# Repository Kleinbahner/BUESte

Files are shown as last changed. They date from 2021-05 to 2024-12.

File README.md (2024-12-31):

# BUESte

## Getting parts:
Parts have been put into Reichelt.de parts baskets. Select a basket, specify the number of times you need the parts and put them in your shopping basket.
The following parts lists are available

- [bue: main pcb](https://www.reichelt.de/my/1827413)
- [bue: button boxes](https://www.reichelt.de/my/1832678)
- [bue: detectors](https://www.reichelt.de/my/1832677)
- [bue: cables](https://www.reichelt.de/my/1832680) select the cables suitable for your setup

Lists are also stored [here](https://github.com/Kleinbahner/BUESte/tree/main/doc/reichelt)

## Manuals:
Manual for main pcb assembly: [main pcb manual](https://github.com/Kleinbahner/BUESte/blob/main/doc/Manual%20(DE)%20Bahn%C3%BCbergang%20Platine%20v2.pdf)

Manual for boxes: [boxes manual](https://github.com/Kleinbahner/BUESte/blob/main/doc/Manual-DE-Box.pdf), [drilling template](https://github.com/Kleinbahner/BUESte/blob/main/doc/drill%20template%20bue.pdf)

Manual for detector: to follow

## Software

Manual for programming the Arduino: [Arduino programming](https://github.com/Kleinbahner/BUESte/blob/main/doc/Programmierung%20Arduino%20f%C3%BCr%20Bahn%C3%BCbergangssteuerung.pdf)

## Components
The railway crossing control unit consists of different components that can can be combined in various ways in order to suit the actual module layout requirements. The components will be described in more detail in the following sections.

### Mainboard

The main board is permanently installed near the railroad crossing. All other components are connected to the main board.

Main board v1 Main board v2

The flashing light signals for the railway crossing and the servos for the fences can be connected via terminal blocks. The control inputs are connected to further terminal blocks. There is also an amplifier for connecting a loudspeaker. The sounds can be stored on a microSD card. Power is supplied via an USB socket.

The two RJ45 sockets are used to connect the other components via a looped-through cable. All components can be connected to the same cable in any order. Star cabling is also possible. Alternatively, the inputs and outputs can also be connected directly to the terminal blocks if they are installed in the same module.

#### Pin assignement
All components must be connected to the main board. It has a number of screw and plug connections for this purpose. Ideally, the main board should be mounted near the railroad crossing itself so that many components such as the flashing signals, the light barrier for clear signaling and the loudspeaker can be connected directly. The following illustration provides an overview of the connection options.

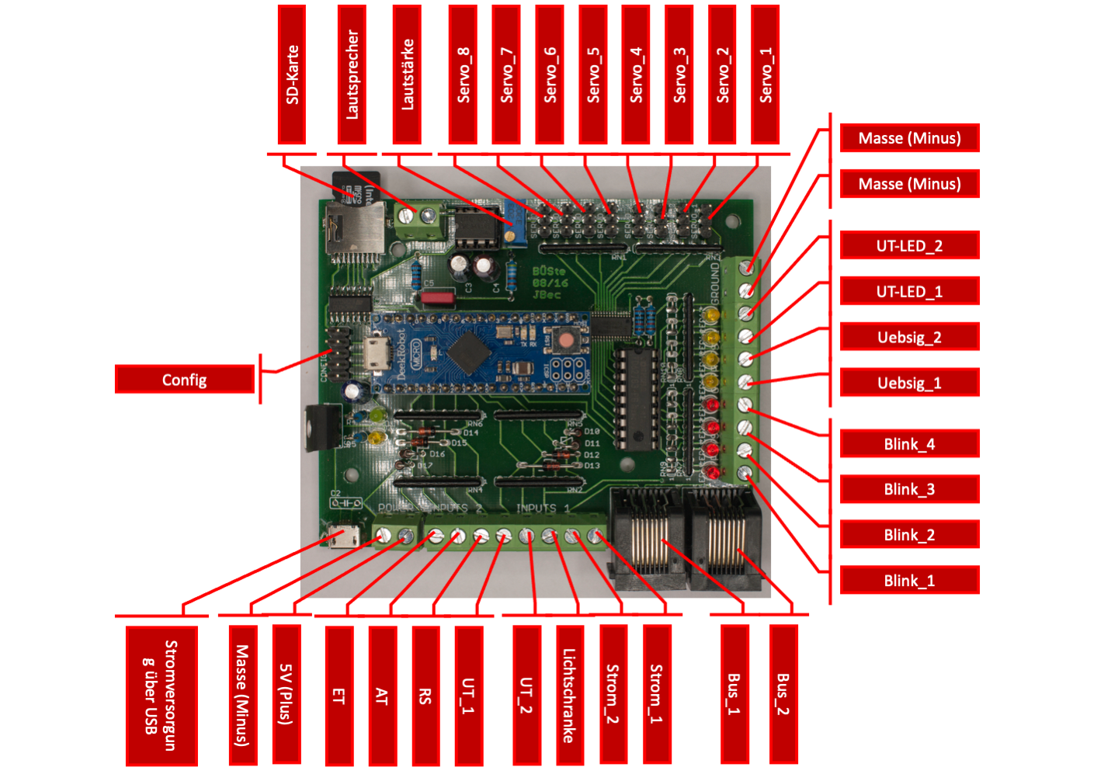
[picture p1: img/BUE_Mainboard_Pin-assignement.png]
Pin assignement main board v1
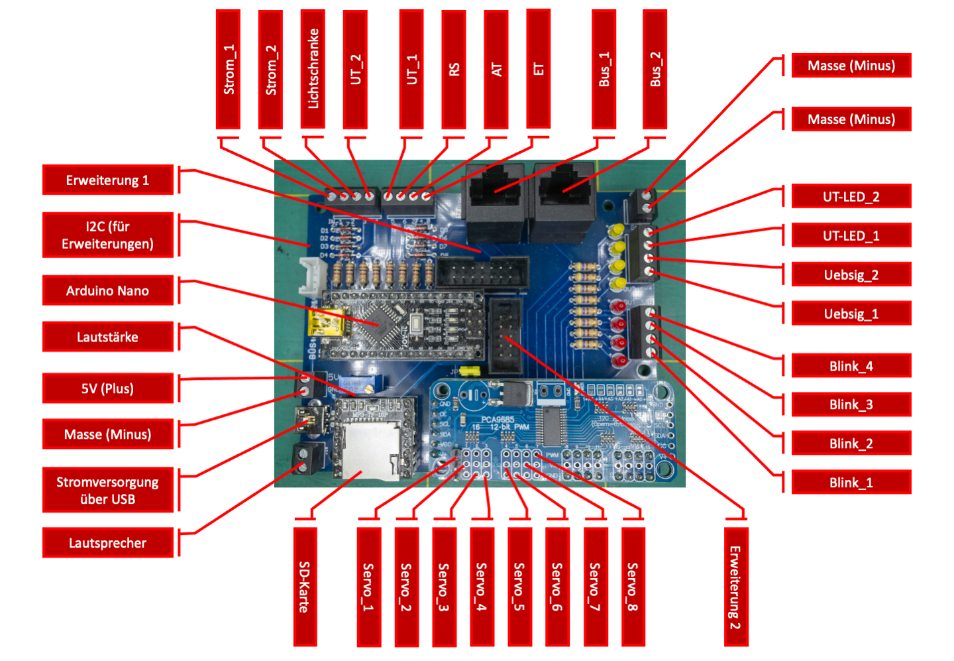
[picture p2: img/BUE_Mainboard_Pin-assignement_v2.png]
Pin assignement main board v2
 

The available signals and their meaning are listed here in detail. The output signals for the LED are driven with 5V. Corresponding series resistors must be added yourself!

| Signal | Direction | Activation | Purpose |
| --- | --- | --- | --- |
| Loudspeaker | output | - | Connections for a small passive loudspeaker, maximum 1W |
| Servo_1 ... Servo_8 | output | Servo connections for the fences. Pin assignement (from boarder of PCB): - , +, pulse |
| UT-LED_1 | output | LED is on if the current sensor on the left track is disabled by the UT push button |
| UT-LED_2 | output | LED is on if the current sensor on the right track is disabled by the UT push button |
| Uebsig_1 | output | LED for the flashing signals of the left track |
| Uebsig_2 | output | LED for the flashing signals of the right track |
| Blink_1 ... Blink_4 | output | Flashing signals for the railroad crossing.  Blink_1 and 2 are phase shifted to Blink_3 and 4 |
| Bus_1 | output | Signals to attached remote components on the left track |
| Bus_2 | output | Signals to attached remote components on the right track |
| Strom_1 | input | LOW active | Input for the current sensor of the left track |
| Strom_2 | input | LOW active | Input for the current sensor of the right track |
| Lichtschranke | input | HIGH active | Input for the light barrier for clear signaling of the railroad crossing |
| UT_1 | input | LOW active | Input to temporary deactivate the current sensor on the left track |
| UT_2 | input | LOW active | Input to temporary deactivate the current sensor on the right track |
| RS | input | LOW active | Input for the "Rangierschalter" (RS) |
| AT | input | LOW active | Input for the disable push button (AT) |
| ET | input | LOW active | Input for the enable push button (ET) |
| USB Power | input | - | Power supply for the circuit. A power bank is recommended to be independent of outlets. |
| 5V | output | - | Supply voltage for light barrier |
| Masse | - | - | Common potential for push buttons |
| Config (only v1_0) | - | - | Actually not used. Can be used for further extensions. |
| I2C (only v2_0) | - | - |  I2C bus of the arudino. For further extensions. |
| Erweiterung 1 (only v2_0) | - | - | Unused pins of the arduino. Actualy not used. |
| Erweiterung 2 (only v2_0) | - | - | Unused pins of the arduino. Actualy not used. |
| SD-Karte | - | - | Slot for SD card. The card has to contain the WAV file for the signal sound. Attention: There has to be a card in the slot with a WAV file called "ding.wav" in the main directory. Otherwise the control unit will not work! |

#### Assignement of the bus cable
A bus is used to connect the components further away from the main board. All the required signals are routed in a single multi-core cable. An RJ45 cable is used for this. Starting from the main board, all components are connected to each other. The boxes have three sockets and can therefore be used as splitters. All sockets are of equal value. The cabling can be carried out in any combination. Only the left and right sections need to be differentiated as the disable buttons, the sensors and the supervision signals are direction dependent. Examples of wiring can be found below under examples.

The socket is assigned as follows (view into the socket):

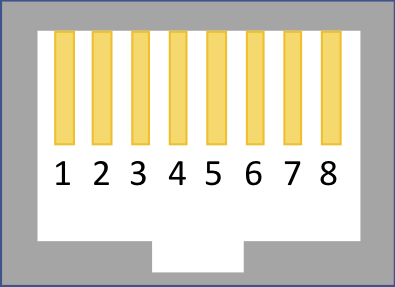
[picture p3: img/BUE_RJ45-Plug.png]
Bus socket


| Pin | Function |
| --- | --- |
| 1 | Ground |
| 2 | Enable push button (ET) |
| 3 | Disable push button (AT) |
| 4 | Shunting switch (RS) |
| 5 | Disable current sensor push button (UT) |
| 6 | LED to mark disabled current sensor |
| 7 | LED for supervision signal. Blinks in phase with flashing light signal |
| 8 | Current sensor |

### Enable box
For manual operation of the railraod crossing a small box is needed. It contains the Enable (ET) and Disable (AT) push buttons as well as a shunting switch. The shunting switch can be equiped with an LED that blinks in phase with the flashing light signal to mark its use.

Einschaltbox

The box can be attached to modules using the well know FREMO-Clamps. The box contains a hole for that purpose.

The connection from the box to the mainboard is through a RJ-45 cable (straight) as it is known from computer networks. Each box has three equal sockets. Thus it can also be used as splitter for cabling.

Backside of box

To ease the cabling inside the box, a small PCB has been designed. It fits perfectly in the boxes used and provides space for three RJ-45 sockets. In addition it provides soldering points for the push buttons and the LEDs.

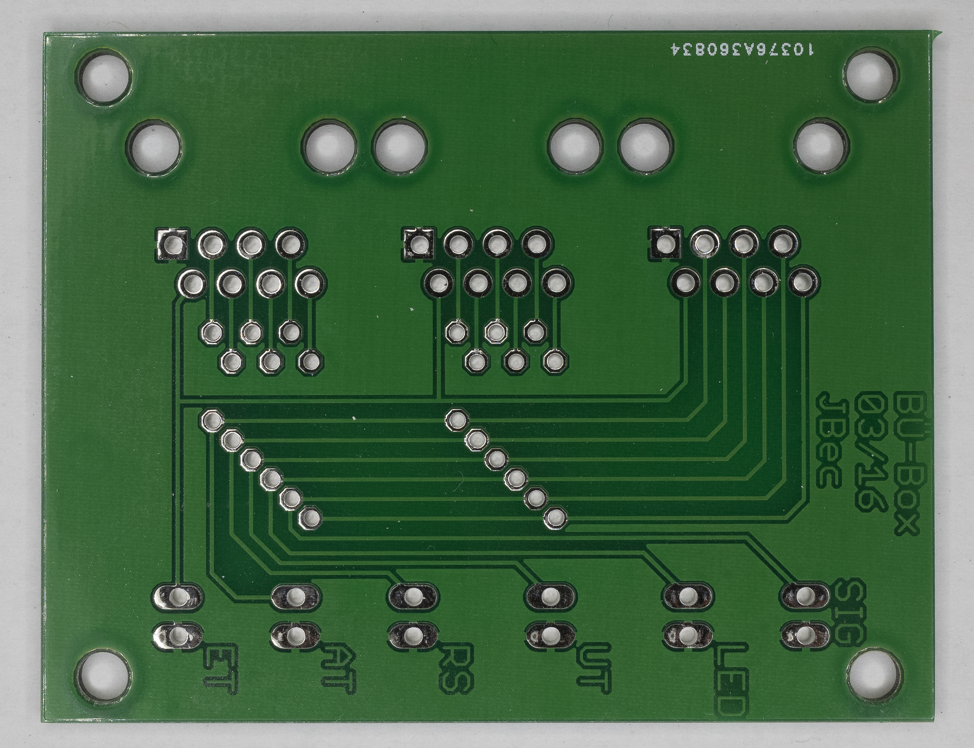
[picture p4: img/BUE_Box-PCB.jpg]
PCB for boxes


### Current sensor
The current sensor is based on the design of Reinhard Müller [http://dcc-mueller.de/wire4dcc/sensor_d.htm](http://dcc-mueller.de/wire4dcc/sensor_d.htm), that has been expanded with a RJ-45 socket for the crossing cabling system.

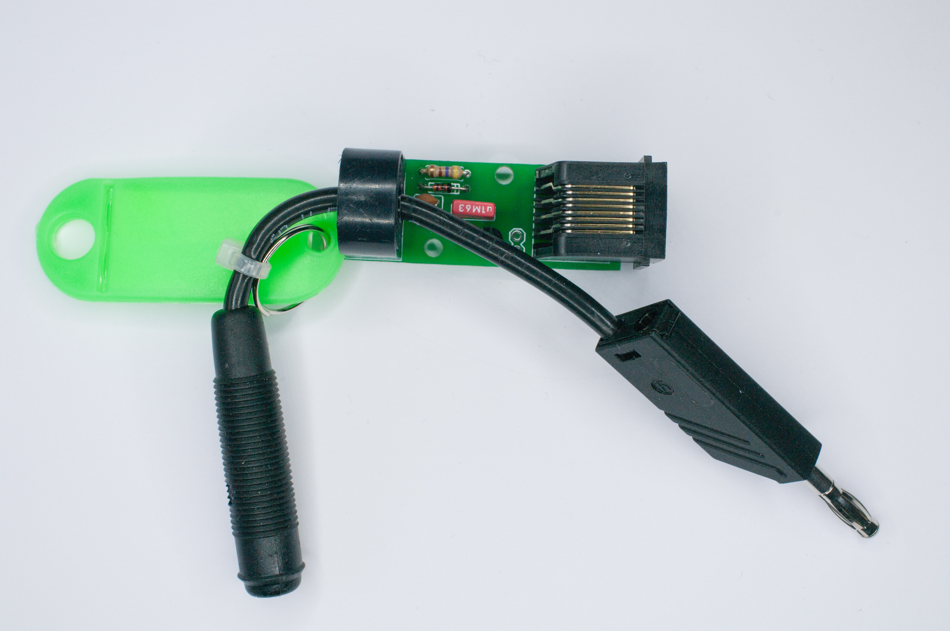
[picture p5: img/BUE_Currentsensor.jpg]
Current sensor


The purpose of the current sensor is the detection of an approaching train. In order to do that one rail of a module is isolated from the neigboring modules (module interconnection cable not pluged in). This rail is then supplied through the current sensor that is attached to the neigboring module. There are no changes of the modules required.

### Sensor box
Near to the current sensor, a sensor box can be attached to the modules using FREMO-clamps. The box can also serve als signal splitter.

Sensor box

The main purpose of this box is to provide the disable button near to the current sensor. By pressing the push button, the current sensor will be disabled for a give time period. A disabled current sensor is signaled by the LED in the box. Deactivation of the sensor can be necessary if there are shunting activities ongoing that would touch the module with the sensor without the need to close the railway crossing.

### Supervision signal
The engine driver needs to know if the railraod crossing is correctly enabled. That is the purpose of the supervision signal that is placed after the current sensor that turns the railroad crossing on. If the railroad crossing is enabled the signal will be blinking.

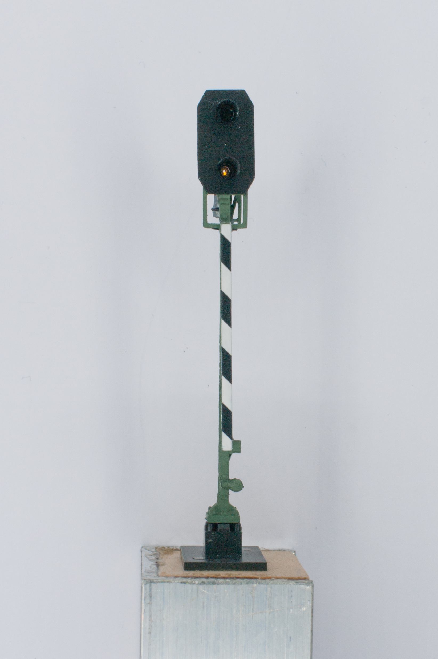
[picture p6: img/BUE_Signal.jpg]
Supervision signal


The supervision signal is placed in a Wattenscheider signal carrier and thus can be placed in any module with the propper Wattenscheiderslot. The signal is connected to the main board using an RJ45-socket. If an additional marker light should be realised, there has to be a sperate power supply. This can for example be done by including a battery and a voltage regulator in the signal carrier.

## Module setup
The components presented before allow for a flexible setup. Two example setups will be presented here.

### Railraod crossing on open track
The most simple case is a railway crossing on clear track. There the main board is integrated in the module which contains the railway crossing and crossing lights. The flashing signal lights, maybe existing fences and the speaker are then directly connected to the main board. Left and right of the railraod crossing on the module at a sufficient distance a sensor module is used. One rail will be isolated from the other modules and will be supplied through a current sensor. The sensor is connected to the main board using RJ45-cables.

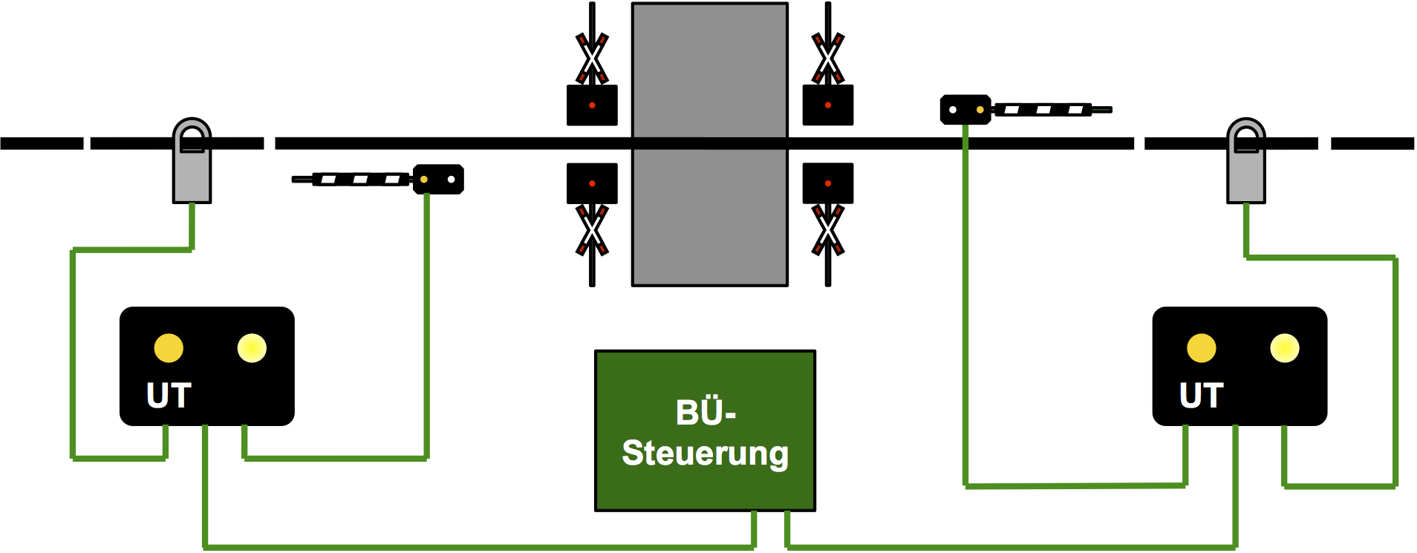
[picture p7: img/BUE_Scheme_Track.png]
Setup at free track


To connect the supervising signals it is recommended to install a sensor box near to every current sensor. The boxes are then used as splitters to connect both the current sensor and the signal.
In this setup the railroad crossing is controlled only by the trains, no interaction of the driver is required.

### Railroad crossing at the end of a station
The situation gets more complex if the railroway crossing is located at the end of a station where trains stop. In this case the railroad crossing can not only be automatically engaged by a current sensor at the side of the station. This could be the case if a train approaches to station to make sure that the crossing is stil secured if the train does not correctly stop at the platform.

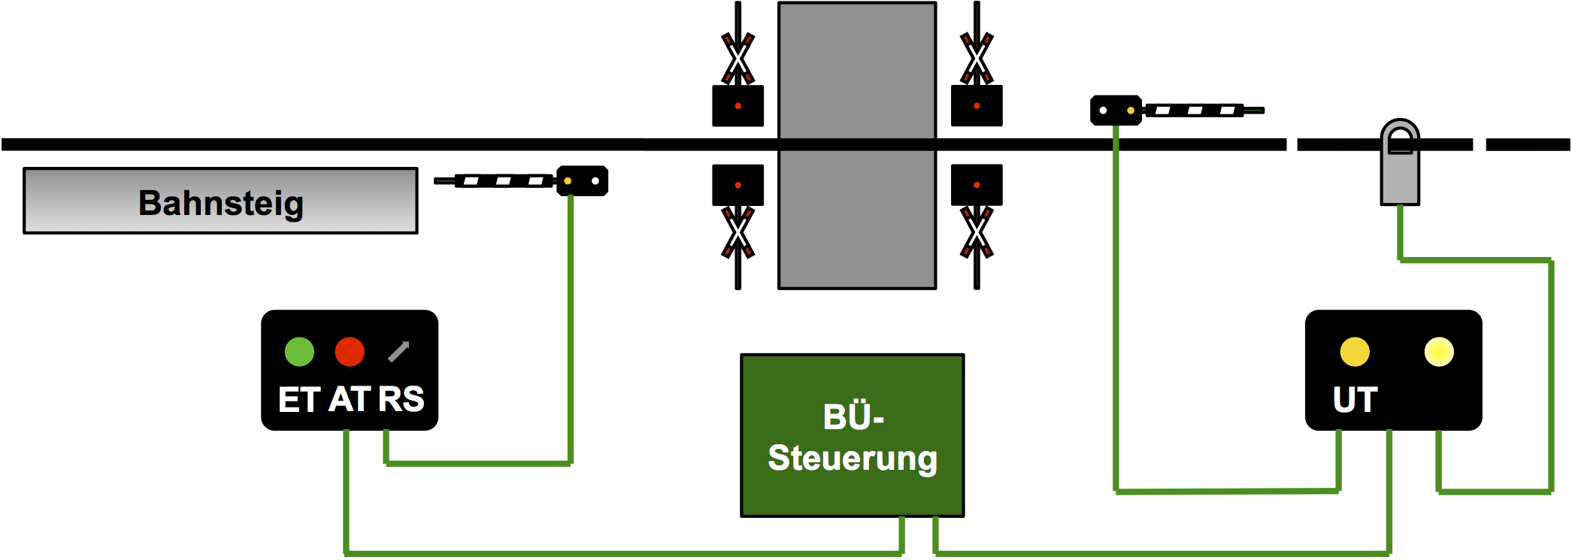
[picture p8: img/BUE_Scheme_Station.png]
Setup in station


As soon as the trains stops, the railway crossing will be deactivated manually using the Einschaltbox to allow road users to use the crossing when the train is stooped at station. Before the trains continue their journey, the crossing has to be enabled again manually. Therefore an Einschaltbox is required.
In addition the box contains the shunting switch. This is switched on if there are shunting activities ongoing that will involve the railway crossing. The lights are then permanently switched on and will only turn off after the shunting switch has been switched off.

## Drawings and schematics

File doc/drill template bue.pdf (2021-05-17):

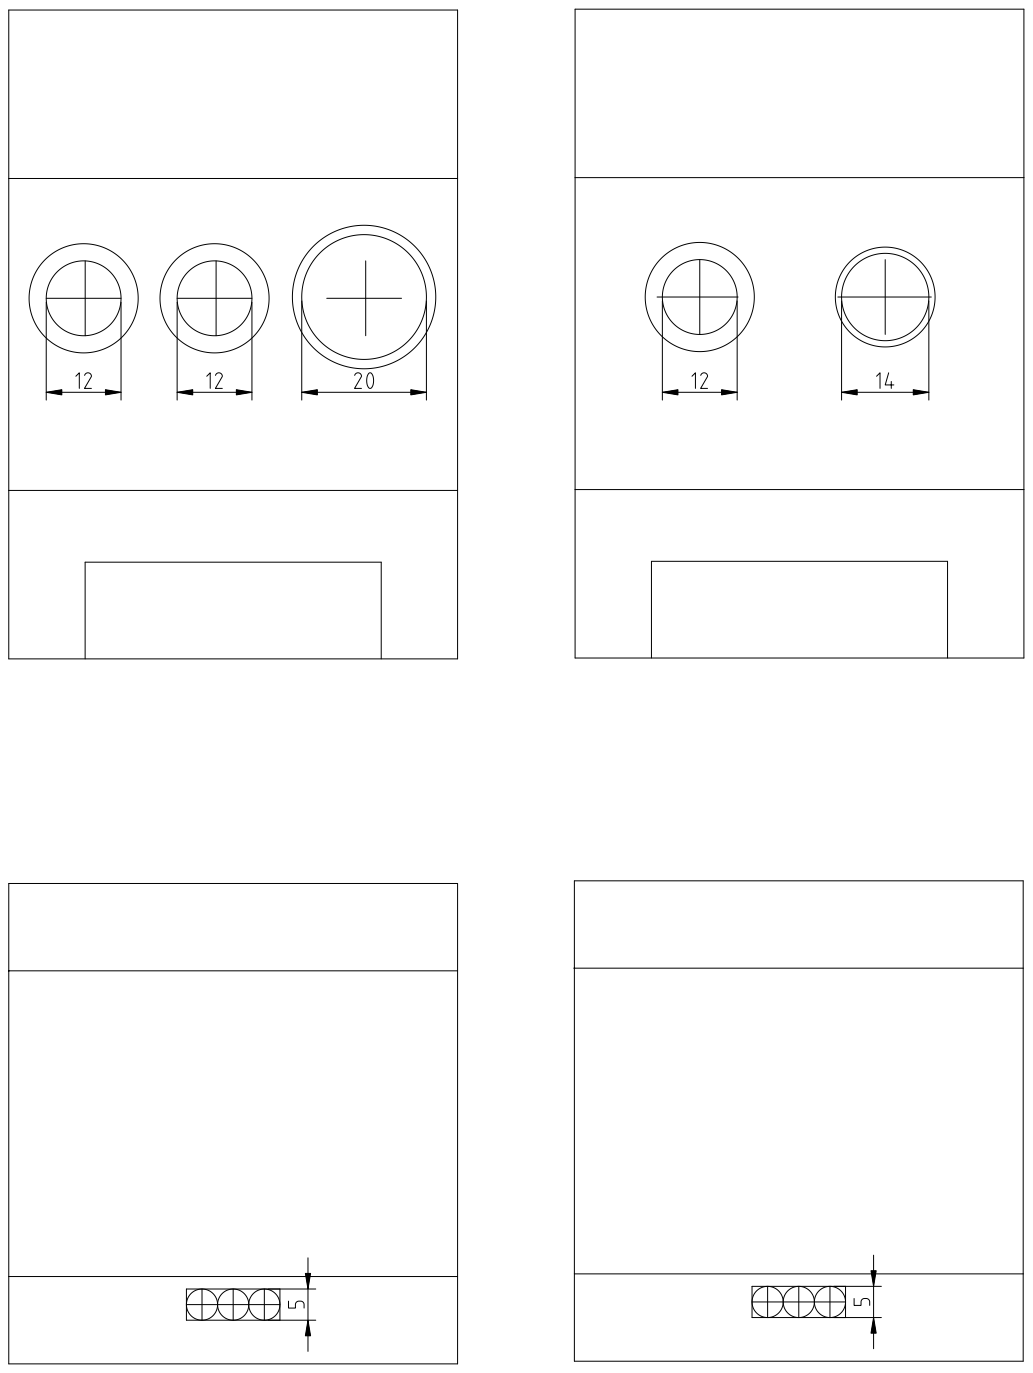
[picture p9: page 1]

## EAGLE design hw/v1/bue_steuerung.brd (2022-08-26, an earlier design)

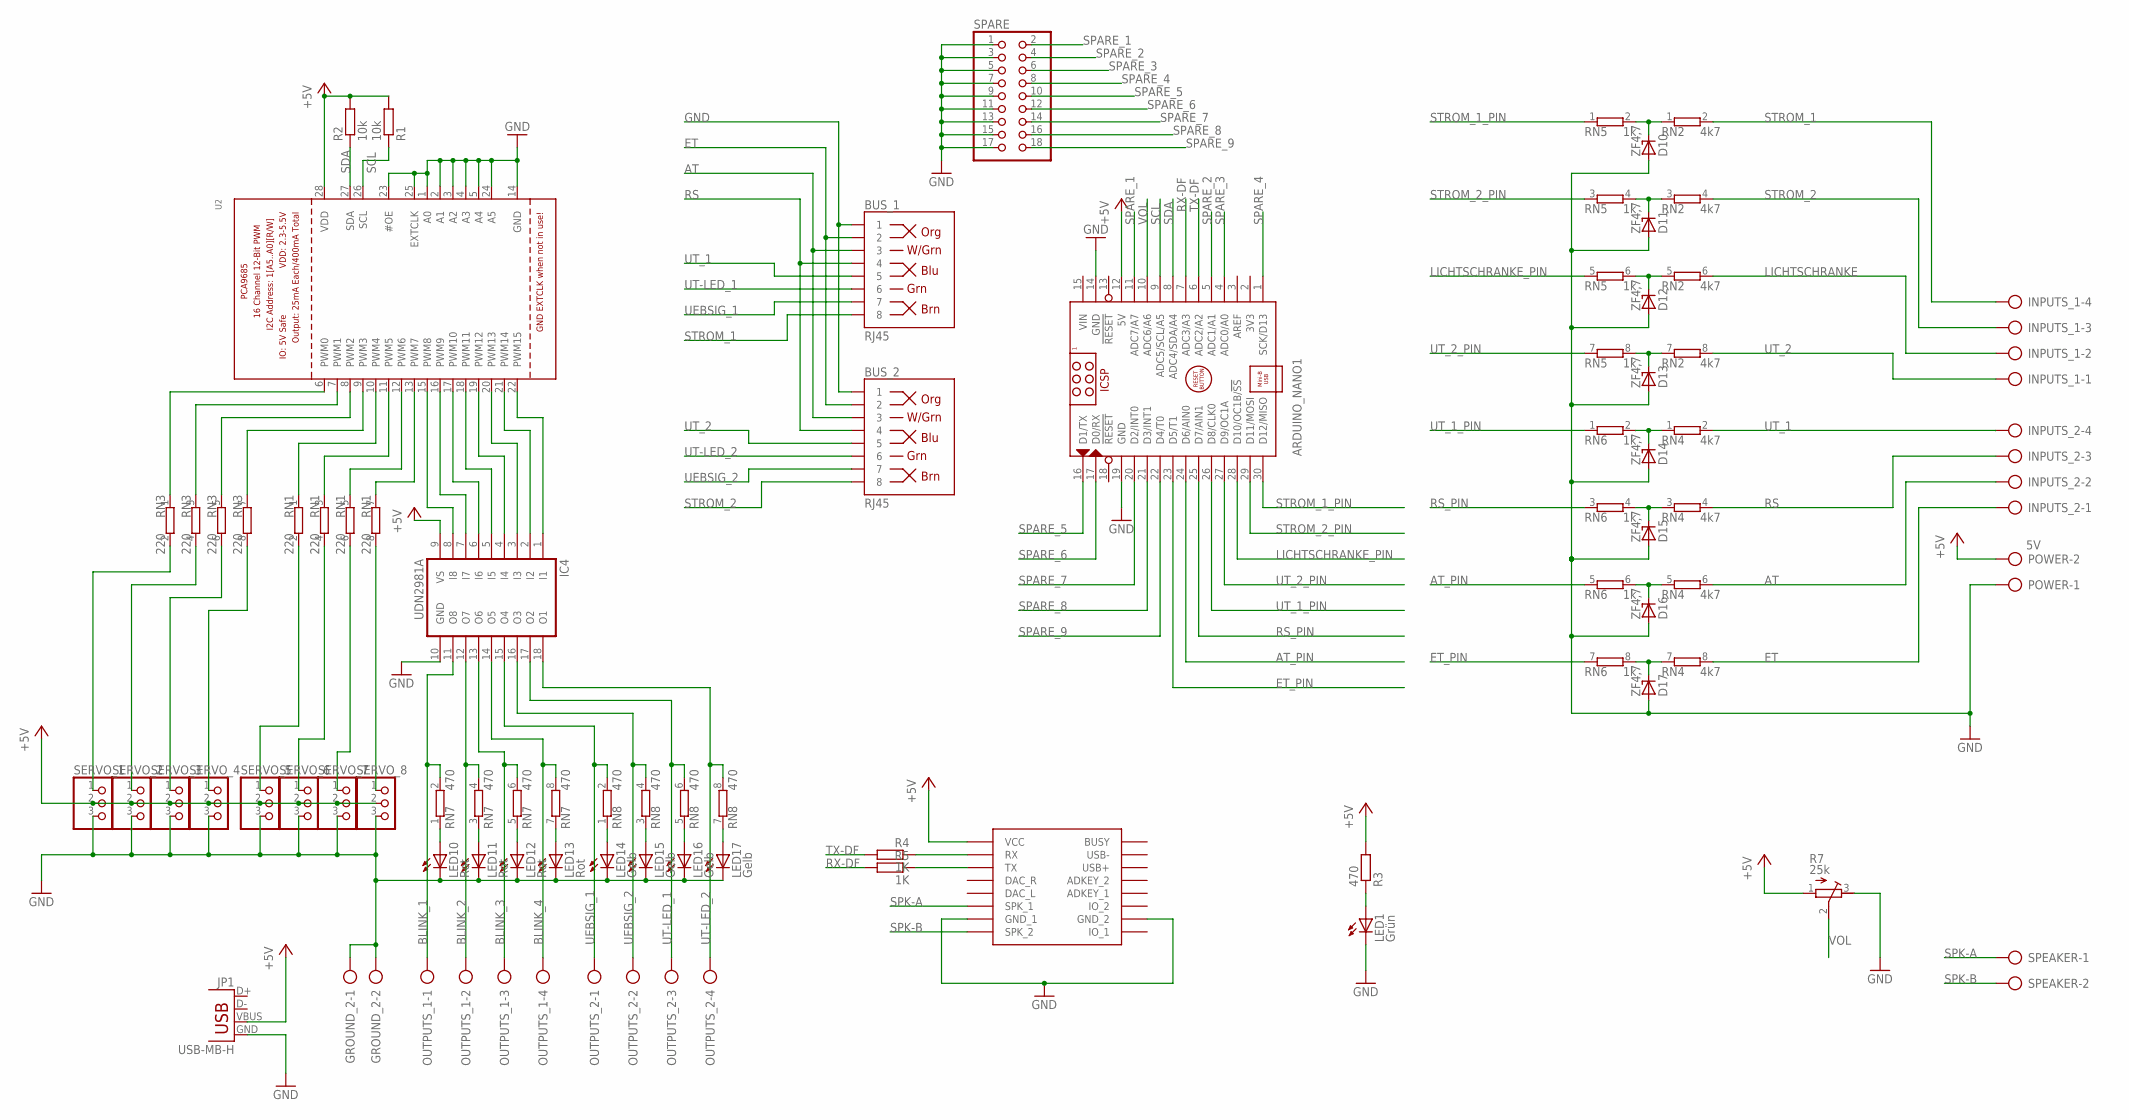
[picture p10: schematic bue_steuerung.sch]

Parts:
ARDUINO_NANO1: ARDUINO_NANO
BUS_1, BUS_2: RJ45; RJ45-8
D10, D17: ZF4,7; ZDIO-2.5
D11, D16: ZF4,7; ZDIO-5
D12, D15: ZF4,7; ZDIO-10
D13, D14: ZF4,7; ZDIO12.5
GROUND_2: AK500/2
IC4: UDN2981A; DIL18
INPUTS_1, INPUTS_2: AK500/4
JP1: USB-MB-H
LED1: Grün; LED3MM
LED10, LED11, LED12, LED13: Rot; LED3MM
LED14, LED15, LED16, LED17: Gelb; LED3MM
OUTPUTS_1, OUTPUTS_2: AK500/4
POWER: 5V; AK500/2
R1, R2: 10k; 0207/10
R3: 470; 0207/10
R4, R5: 1K; 0207/10
R7: 25k; RTRIM64Z
RN1, RN3: 220; SIL8
RN2, RN4: 4k7; SIL8
RN5, RN6: 1k; SIL8
RN7, RN8: 470; SIL8
SERVO_1, SERVO_2, SERVO_3, SERVO_4, SERVO_5, SERVO_6, SERVO_7, SERVO_8: PINHD-1X3; 1X03
SPARE: PINHD-2X9; 2X09
SPEAKER: AK500/2
U2: PCA9685; TSSOP28
U$1: DFPLAYER

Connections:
+5V: ARDUINO_NANO1.12 (5V), IC4.9 (VS), JP1.VBUS, POWER.2, R1.2, R2.2, R3.2, R7.1 (E), SERVO_1.2, SERVO_2.2, SERVO_3.2, SERVO_4.2, SERVO_5.2, SERVO_6.2, SERVO_7.2, SERVO_8.2, U2.28 (VDD), U$1.VCC
AT: BUS_1.3, BUS_2.3, INPUTS_2.2, RN4.6 (2)
AT_PIN: ARDUINO_NANO1.24 (D6/AIN0), RN6.5 (1)
BLINK_1: IC4.11 (O8), OUTPUTS_1.1, RN7.2
BLINK_2: IC4.12 (O7), OUTPUTS_1.2, RN7.4 (2)
BLINK_3: IC4.13 (O6), OUTPUTS_1.3, RN7.6 (2)
BLINK_4: IC4.14 (O5), OUTPUTS_1.4, RN7.8 (2)
ET: BUS_1.2, BUS_2.2, INPUTS_2.1, RN4.8 (2)
ET_PIN: ARDUINO_NANO1.23 (D5/T1), RN6.7 (1)
GND: ARDUINO_NANO1.14 (GND), ARDUINO_NANO1.19 (GND), BUS_1.1, BUS_2.1, D10.A, D11.A, D12.A, D13.A, D14.A, D15.A, D16.A, D17.A, GROUND_2.1, GROUND_2.2, IC4.10 (GND), JP1.GND, LED1.K (C), LED10.K (C), LED11.K (C), LED12.K (C), LED13.K (C), LED14.K (C), LED15.K (C), LED16.K (C), LED17.K (C), POWER.1, R7.3 (A), SERVO_1.3, SERVO_2.3, SERVO_3.3, SERVO_4.3, SERVO_5.3, SERVO_6.3, SERVO_7.3, SERVO_8.3, SPARE.1, SPARE.3, SPARE.5, SPARE.7, SPARE.9, SPARE.11, SPARE.13, SPARE.15, SPARE.17, U2.1 (A0), U2.2 (A1), U2.3 (A2), U2.4 (A3), U2.5 (A4), U2.14 (GND), U2.23 (#OE), U2.24 (A5), U2.25 (EXTCLK), U$1.GND_1, U$1.GND_2
LICHTSCHRANKE: INPUTS_1.2, RN2.6 (2)
LICHTSCHRANKE_PIN: ARDUINO_NANO1.28 (D10/OC1B/!SS), RN5.5 (1)
unnamed: RN1.4 (2), SERVO_6.1
unnamed: RN1.6 (2), SERVO_7.1
unnamed: RN1.8 (2), SERVO_8.1
unnamed: IC4.8 (I8), U2.15 (PWM8)
unnamed: LED14.A, RN8.1
unnamed: LED1.A, R3.1
unnamed: R4.1, U$1.RX
unnamed: IC4.7 (I7), U2.16 (PWM9)
unnamed: R5.1, U$1.TX
unnamed: D17.C, RN4.7 (1), RN6.8 (2)
unnamed: D14.C, RN4.1, RN6.2
unnamed: D16.C, RN4.5 (1), RN6.6 (2)
unnamed: D15.C, RN4.3 (1), RN6.4 (2)
unnamed: D12.C, RN2.5 (1), RN5.6 (2)
unnamed: D11.C, RN2.3 (1), RN5.4 (2)
unnamed: D10.C, RN2.1, RN5.2
unnamed: D13.C, RN2.7 (1), RN5.8 (2)
unnamed: IC4.6 (I6), U2.17 (PWM10)
unnamed: IC4.5 (I5), U2.18 (PWM11)
unnamed: IC4.4 (I4), U2.19 (PWM12)
unnamed: IC4.3 (I3), U2.20 (PWM13)
unnamed: RN3.2, SERVO_1.1
unnamed: RN3.4 (2), SERVO_2.1
unnamed: RN3.6 (2), SERVO_3.1
unnamed: RN3.8 (2), SERVO_4.1
unnamed: RN1.2, SERVO_5.1
unnamed: IC4.2 (I2), U2.21 (PWM14)
unnamed: IC4.1 (I1), U2.22 (PWM15)
unnamed: LED10.A, RN7.1
unnamed: LED11.A, RN7.3 (1)
unnamed: LED12.A, RN7.5 (1)
unnamed: RN3.1, U2.6 (PWM0)
unnamed: RN3.3 (1), U2.7 (PWM1)
unnamed: RN3.5 (1), U2.8 (PWM2)
unnamed: RN3.7 (1), U2.9 (PWM3)
unnamed: RN1.1, U2.10 (PWM4)
unnamed: RN1.3 (1), U2.11 (PWM5)
unnamed: RN1.5 (1), U2.12 (PWM6)
unnamed: RN1.7 (1), U2.13 (PWM7)
unnamed: LED13.A, RN7.7 (1)
unnamed: LED15.A, RN8.3 (1)
unnamed: LED16.A, RN8.5 (1)
unnamed: LED17.A, RN8.7 (1)
RS: BUS_1.4, BUS_2.4, INPUTS_2.3, RN4.4 (2)
RS_PIN: ARDUINO_NANO1.25 (D7/AIN1), RN6.3 (1)
RX-DF: ARDUINO_NANO1.7 (ADC3/A3), R5.2
SCL: ARDUINO_NANO1.9 (ADC5/SCL/A5), R1.1, U2.26 (SCL)
SDA: ARDUINO_NANO1.8 (ADC4/SDA/A4), R2.1, U2.27 (SDA)
SPARE_1: ARDUINO_NANO1.11 (ADC7/A7), SPARE.2
SPARE_2: ARDUINO_NANO1.5 (ADC1/A1), SPARE.4
SPARE_3: ARDUINO_NANO1.4 (ADC0/A0), SPARE.6
SPARE_4: ARDUINO_NANO1.1 (SCK/D13), SPARE.8
SPARE_5: ARDUINO_NANO1.16 (D1/TX), SPARE.10
SPARE_6: ARDUINO_NANO1.17 (D0/RX), SPARE.12
SPARE_7: ARDUINO_NANO1.20 (D2/INT0), SPARE.14
SPARE_8: ARDUINO_NANO1.21 (D3/INT1), SPARE.16
SPARE_9: ARDUINO_NANO1.22 (D4/T0), SPARE.18
SPK-A: SPEAKER.1, U$1.SPK1 (SPK_1)
SPK-B: SPEAKER.2, U$1.SPK2 (SPK_2)
STROM_1: BUS_1.8, INPUTS_1.4, RN2.2
STROM_1_PIN: ARDUINO_NANO1.30 (D12/MISO), RN5.1
STROM_2: BUS_2.8, INPUTS_1.3, RN2.4 (2)
STROM_2_PIN: ARDUINO_NANO1.29 (D11/MOSI), RN5.3 (1)
TX-DF: ARDUINO_NANO1.6 (ADC2/A2), R4.2
UEBSIG_1: BUS_1.7, IC4.15 (O4), OUTPUTS_2.1, RN8.2
UEBSIG_2: BUS_2.7, IC4.16 (O3), OUTPUTS_2.2, RN8.4 (2)
UT-LED_1: BUS_1.6, IC4.17 (O2), OUTPUTS_2.3, RN8.6 (2)
UT-LED_2: BUS_2.6, IC4.18 (O1), OUTPUTS_2.4, RN8.8 (2)
UT_1: BUS_1.5, INPUTS_2.4, RN4.2
UT_1_PIN: ARDUINO_NANO1.26 (D8/CLK0), RN6.1
UT_2: BUS_2.5, INPUTS_1.1, RN2.8 (2)
UT_2_PIN: ARDUINO_NANO1.27 (D9/OC1A), RN5.7 (1)
VIN: ARDUINO_NANO1.15 (VIN)
VOL: ARDUINO_NANO1.10 (ADC6/A6), R7.2 (S)

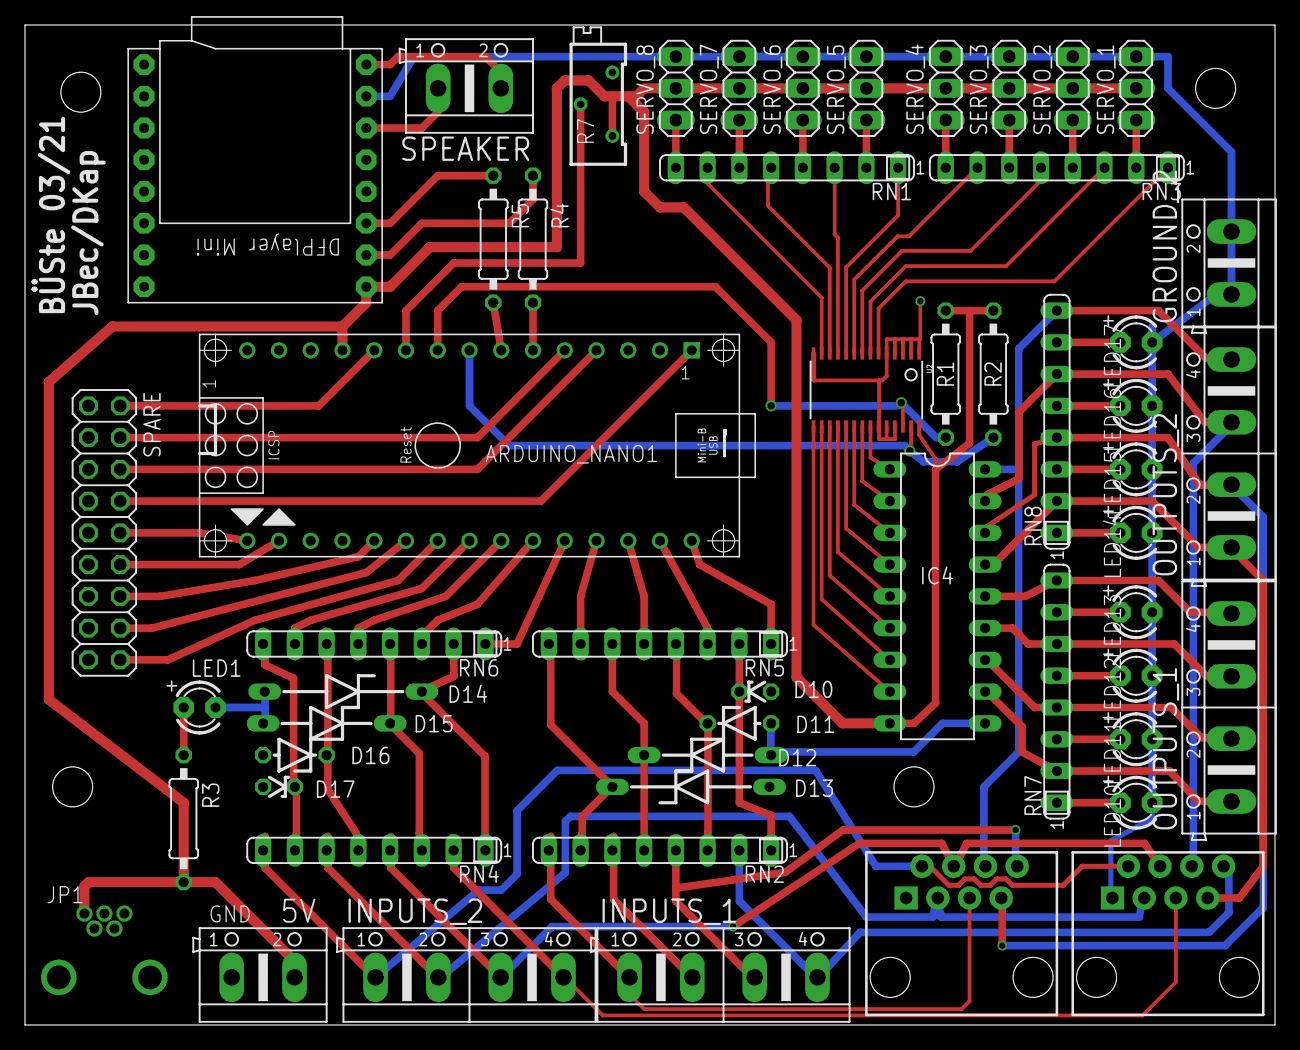
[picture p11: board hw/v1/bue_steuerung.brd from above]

Board: 2 copper layers, 100.0 x 80.0 mm, 54 parts (0 on the bottom side), 85 nets.

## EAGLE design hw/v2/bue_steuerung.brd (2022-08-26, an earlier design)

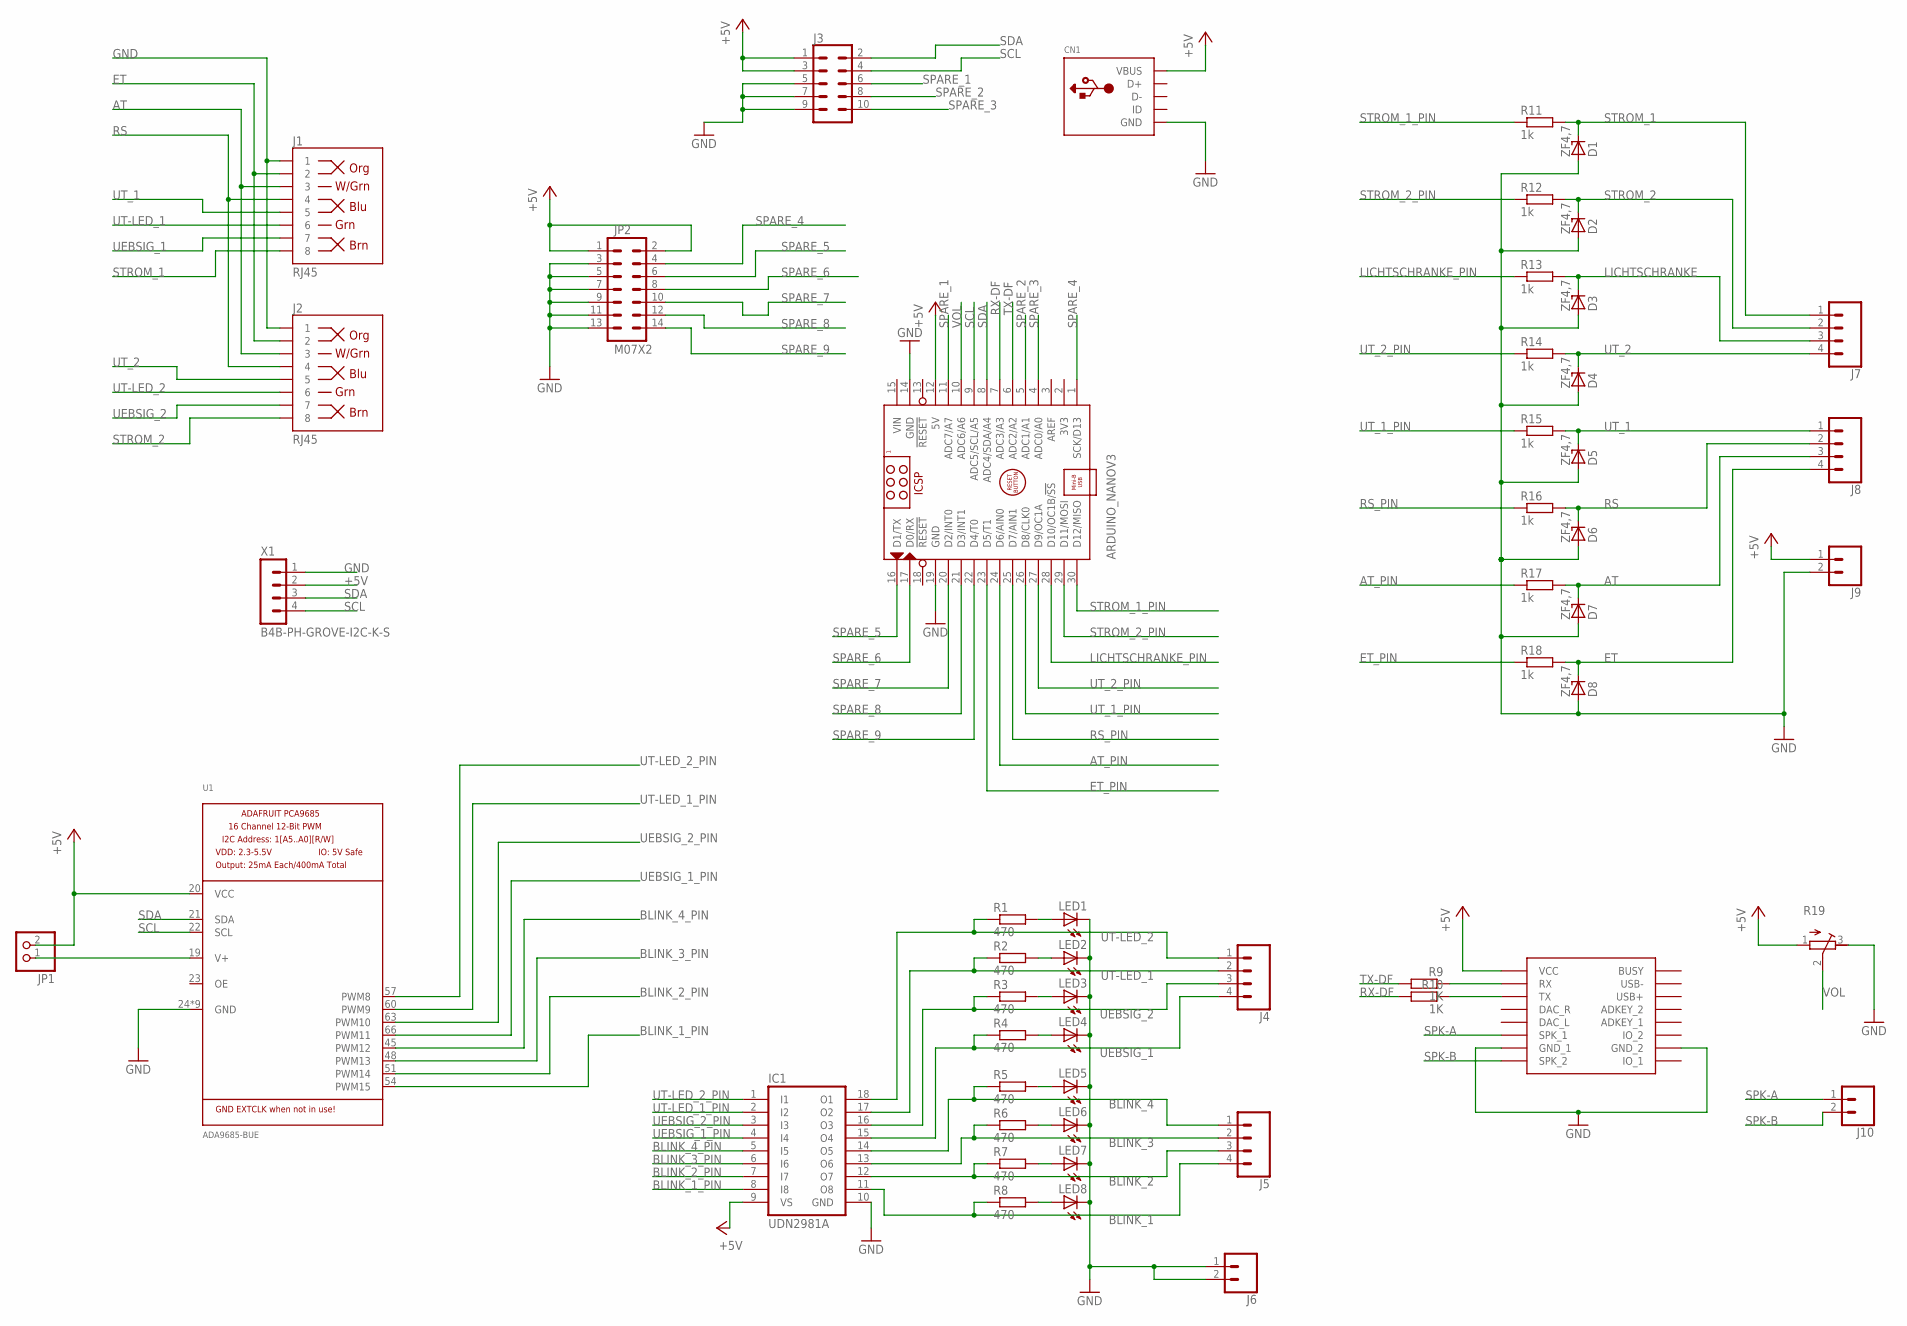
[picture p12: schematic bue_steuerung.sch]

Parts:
ARDUINO_NANOV3: ARDUINO_NANO
CN1: USBMOLEX; USB-MINIB-THM-MOLEX
D1, D2, D3, D4, D5, D6, D7, D8: ZF4,7; ZDIO-7.5
IC1: UDN2981A; DIL18
J1, J2: RJ45; RJ45-8
J3: CONN_05X2SHD; 2X5-SHROUDED
J4, J5, J7, J8: CONN_04SCREW; SCREWTERMINAL-3.5MM-4
J6, J9, J10: CONN_023.5MM; SCREWTERMINAL-3.5MM-2
JP1: PINHD-1X2; 1X02
JP2: M07X2; 2X7-SHROUDED
LED1, LED2, LED3, LED4, LED5, LED6, LED7, LED8: LED3MM
R1, R2, R3, R4, R5, R6, R7, R8: 470; 0207/7
R9, R10: 1K; 0207/7
R11, R12, R13, R14, R15, R16, R17, R18: 1k; 0207/7
R19: R-TRIMM64Y; RTRIM64Y
U1: ADA9685-BUE
U2: DFPLAYER
X1: B4B-PH-GROVE-I2C-K-S; B4B-PH-K-S

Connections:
+5V: ARDUINO_NANOV3.12 (5V), CN1.VBUS, IC1.9 (VS), J3.1, J3.3, J9.1, JP1.2, JP2.1, JP2.2, R19.1 (A), U1.20 (VCC), U2.VCC, X1.2 (3)
AT: D7.C, J1.3, J2.3, J8.3, R17.2
AT_PIN: ARDUINO_NANOV3.24 (D6/AIN0), R17.1
BLINK_1: IC1.11 (O8), J5.4, R8.1
BLINK_1_PIN: IC1.8 (I8), U1.54 (PWM15)
BLINK_2: IC1.12 (O7), J5.3, R7.1
BLINK_2_PIN: IC1.7 (I7), U1.51 (PWM14)
BLINK_3: IC1.13 (O6), J5.2, R6.1
BLINK_3_PIN: IC1.6 (I6), U1.48 (PWM13)
BLINK_4: IC1.14 (O5), J5.1, R5.1
BLINK_4_PIN: IC1.5 (I5), U1.45 (PWM12)
ET: D8.C, J1.2, J2.2, J8.4, R18.2
ET_PIN: ARDUINO_NANOV3.23 (D5/T1), R18.1
GND: ARDUINO_NANOV3.14 (GND), ARDUINO_NANOV3.19 (GND), CN1.GND, D1.A, D2.A, D3.A, D4.A, D5.A, D6.A, D7.A, D8.A, IC1.10 (GND), J1.1, J2.1, J3.5, J3.7, J3.9, J6.1, J6.2, J9.2, JP2.3, JP2.5, JP2.7, JP2.9, JP2.11, JP2.13, LED1.K (C), LED2.K (C), LED3.K (C), LED4.K (C), LED5.K (C), LED6.K (C), LED7.K (C), LED8.K (C), R19.3 (E), U1.24 (GND), U1.43 (GND), U1.46 (GND), U1.49 (GND), U1.52 (GND), U1.55 (GND), U1.58 (GND), U1.61 (GND), U1.64 (GND), U2.GND_1, U2.GND_2, X1.1 (4)
LICHTSCHRANKE: D3.C, J7.3, R13.2
LICHTSCHRANKE_PIN: ARDUINO_NANOV3.28 (D10/OC1B/!SS), R13.1
unnamed: JP1.1, U1.19 (V+)
unnamed: LED4.A, R4.2
unnamed: R9.1, U2.RX
unnamed: R10.1, U2.TX
unnamed: LED8.A, R8.2
unnamed: LED7.A, R7.2
unnamed: LED6.A, R6.2
unnamed: LED5.A, R5.2
unnamed: LED3.A, R3.2
unnamed: LED2.A, R2.2
unnamed: LED1.A, R1.2
RS: D6.C, J1.4, J2.4, J8.2, R16.2
RS_PIN: ARDUINO_NANOV3.25 (D7/AIN1), R16.1
RX-DF: ARDUINO_NANOV3.7 (ADC3/A3), R10.2
SCL: ARDUINO_NANOV3.9 (ADC5/SCL/A5), J3.4, U1.22 (SCL), X1.4 (1)
SDA: ARDUINO_NANOV3.8 (ADC4/SDA/A4), J3.2, U1.21 (SDA), X1.3 (2)
SPARE_1: ARDUINO_NANOV3.11 (ADC7/A7), J3.6
SPARE_2: ARDUINO_NANOV3.5 (ADC1/A1), J3.8
SPARE_3: ARDUINO_NANOV3.4 (ADC0/A0), J3.10
SPARE_4: ARDUINO_NANOV3.1 (SCK/D13), JP2.4
SPARE_5: ARDUINO_NANOV3.16 (D1/TX), JP2.6
SPARE_6: ARDUINO_NANOV3.17 (D0/RX), JP2.8
SPARE_7: ARDUINO_NANOV3.20 (D2/INT0), JP2.10
SPARE_8: ARDUINO_NANOV3.21 (D3/INT1), JP2.12
SPARE_9: ARDUINO_NANOV3.22 (D4/T0), JP2.14
SPK-A: J10.1, U2.SPK1 (SPK_1)
SPK-B: J10.2, U2.SPK2 (SPK_2)
STROM_1: D1.C, J1.8, J7.1, R11.2
STROM_1_PIN: ARDUINO_NANOV3.30 (D12/MISO), R11.1
STROM_2: D2.C, J2.8, J7.2, R12.2
STROM_2_PIN: ARDUINO_NANOV3.29 (D11/MOSI), R12.1
TX-DF: ARDUINO_NANOV3.6 (ADC2/A2), R9.2
UEBSIG_1: IC1.15 (O4), J1.7, J4.4, R4.1
UEBSIG_1_PIN: IC1.4 (I4), U1.66 (PWM11)
UEBSIG_2: IC1.16 (O3), J2.7, J4.3, R3.1
UEBSIG_2_PIN: IC1.3 (I3), U1.63 (PWM10)
UT-LED_1: IC1.17 (O2), J1.6, J4.2, R2.1
UT-LED_1_PIN: IC1.2 (I2), U1.60 (PWM9)
UT-LED_2: IC1.18 (O1), J2.6, J4.1, R1.1
UT-LED_2_PIN: IC1.1 (I1), U1.57 (PWM8)
UT_1: D5.C, J1.5, J8.1, R15.2
UT_1_PIN: ARDUINO_NANOV3.26 (D8/CLK0), R15.1
UT_2: D4.C, J2.5, J7.4, R14.2
UT_2_PIN: ARDUINO_NANOV3.27 (D9/OC1A), R14.1
VIN: ARDUINO_NANOV3.15 (VIN)
VOL: ARDUINO_NANOV3.10 (ADC6/A6), R19.2 (S)

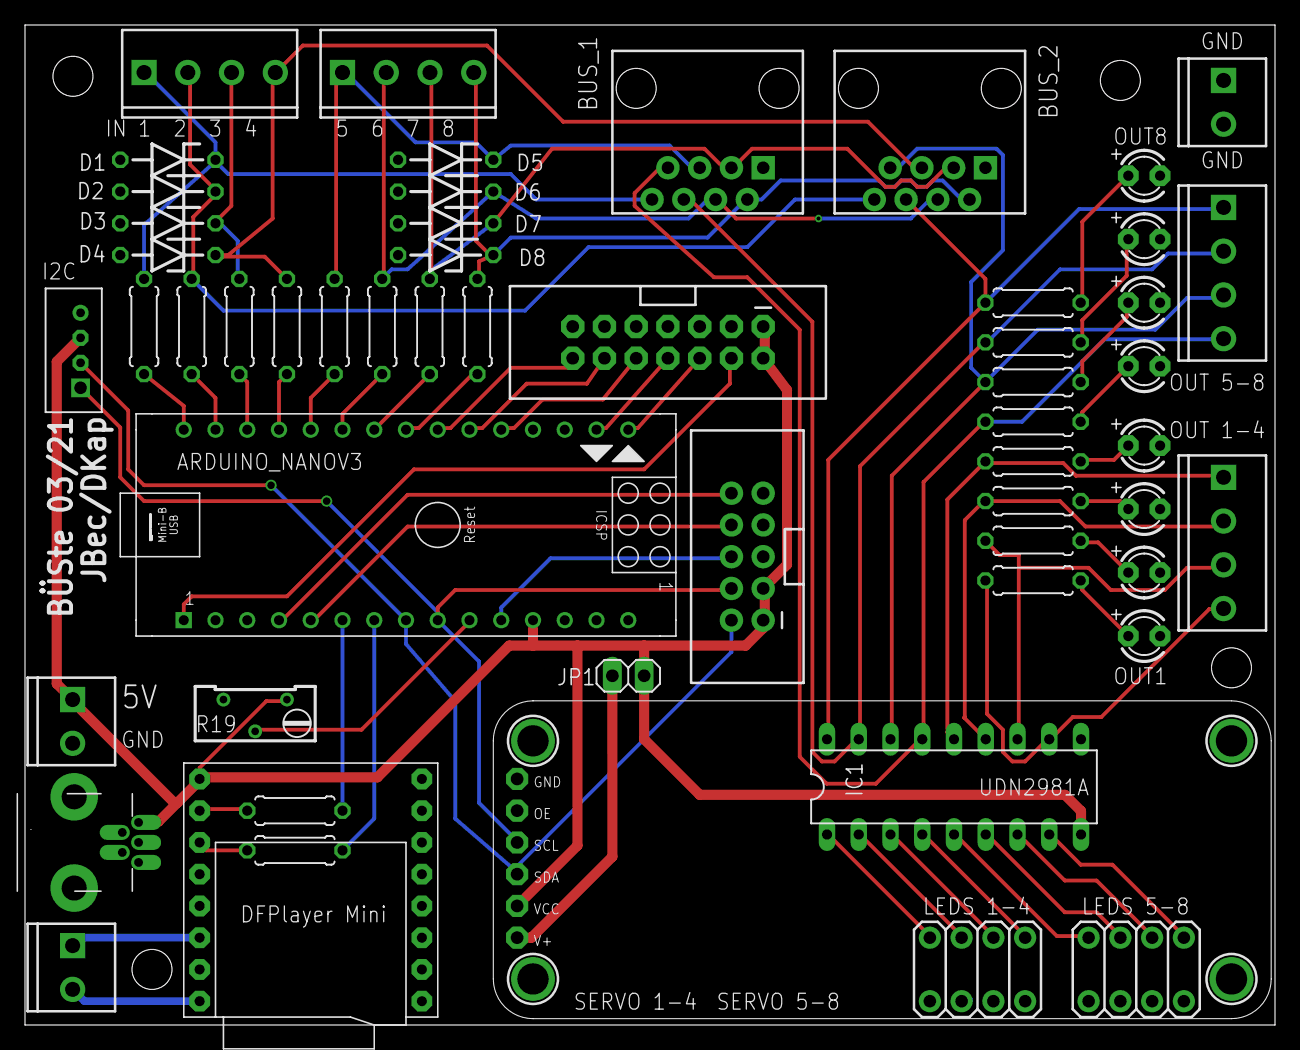
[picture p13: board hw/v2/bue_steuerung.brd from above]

Board: 2 copper layers, 100.0 x 80.0 mm, 53 parts (0 on the bottom side), 61 nets.

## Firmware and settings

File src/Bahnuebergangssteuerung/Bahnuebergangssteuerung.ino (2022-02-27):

/* Bahnuebergangsteuerung v2.1.4 (C) Jens Becker
 *  
 *  Unterstützt nur die Hardware Version 03/21 der Bahnübergangssteuerung BÜSte
 *  
 *  Treiber fuer den PWM-Chip von Adafruit https://github.com/adafruit/Adafruit-PWM-Servo-Driver-Library/archive/master.zip
 * 
 *  Debouncing der Tasten mit der Bounce2 Bibliothek https://github.com/thomasfredericks/Bounce2
 *
 *  Audiowiedergabe über DFPlayer mini MP3-Modul mit Bibliothek PowerBroker2 https://github.com/PowerBroker2/DFPlayerMini_Fast
 * 
 *  DFlayerMini_Fast library requires FireTimer lib https://github.com/PowerBroker2/FireTimer
 *
 *  storing EEPROM values requires CRC32 library  *https://downloads.arduino.cc/libraries/github.com/bakercp/CRC32-2.0.0.zip // Disabled DKap
*/
//##########################################################################
//#
//#   Version History:
//#
//#-------------------------------------------------------------------------
//#
//#  Version: 2.1.4 date: 2022/02/27 author: JBec
//#
//# Added:
//#   - Changed Deboucing-Lib to Button2 
//#     https://github.com/thomasfredericks/Bounce2
//#   - Removed forced Servo setup if EEPROM data was wrong
//#   - LED test at startup
//#
//#-------------------------------------------------------------------------
//#
//#  Version: 2.1.3 date: 2021/10/16 author: DKap
//#
//# Added:
//#   - DFFast driver, for other models DFmini is required
//#     --> #define DFFast
//#
//#-------------------------------------------------------------------------
//#
//#  Version: 2.1.2 date: 2021/04/20 author: DKap
//#
//# Added:
//#   - delay Schranke implemended
//#
//#-------------------------------------------------------------------------
//#
//#  Version: 2.1.2 date: 2021/04/19 author: DKap
//#
//# Added:
//#   - UT2 also detected on servo setup
//#   - Servo setup also scalable up to 4 servos with indication of which 
//#     setting on the other 4 LED
//#
//#-------------------------------------------------------------------------
//#
//#  Version: 2.1.2 date: 2021/04/18 author: DKap
//#
//# Added:
//#   - Servo variables scalable by changing NUM_OF_SCHRANKEN, no code
//#     change necessary
//#
//#-------------------------------------------------------------------------
//#
//#  Version: 2.1.2 date: 2021/04/15 author: DKap
//#
//# Added:
//#   - removed CRC from EEPROM storing
//#
//#-------------------------------------------------------------------------


const int VERSION_MAJOR = 2;
const int VERSION_MINOR = 1;
const int VERSION_PATCH = 4;

//==========================================================================
//
//    I N C L U D E S
//
//==========================================================================

#include <EEPROM.h>

#include <avr/pgmspace.h> // Wird zum Ablegen von Werten im FLASH benoetigt

// PWM-Driver for PCA9685
#include <Wire.h>
#include <Adafruit_PWMServoDriver.h>

// Debouncing of inputs
#include <Bounce2.h>

// CRC32 1.1.0 (Christopher Baker)
#include <CRC32.h>

// Uncomment if sound is not working
//#define DFFast

// DFPlayer mini fast
#ifdef DFFast
  #include <DFPlayerMini_Fast.h>
#else
  #include <DFRobotDFPlayerMini.h>
#endif
#include <SoftwareSerial.h>


//==========================================================================
//
//    D E F I N I T I O N S
//
//==========================================================================

// enable Debug-Output on serial interface
#define DEBUG

#ifdef DEBUG
 #define DEBUG_PRINT(x)     Serial.print (x)
 #define DEBUG_PRINTDEC(x)     Serial.print (x, DEC)
 #define DEBUG_PRINTLN(x)  Serial.println (x)
#else
 #define DEBUG_PRINT(x)
 #define DEBUG_PRINTDEC(x)
 #define DEBUG_PRINTLN(x) 
#endif

#define SW_VERSION 1  // For EEPROM data, data will be set to default value is not the same

// Ausgangspins
#define blink1_OUT 15     // hier wird das erste Blinklicht angeschlossen
#define blink2_OUT 14     // hier wird das zweite Blinklicht angeschlossen
#define blink3_OUT 13     // hier wird das dritte Blinklicht angeschlossen
#define blink4_OUT 12     // hier wird das vierte Blinklicht angeschlossen
#define uebsig1_OUT 11    // hier wird das rechte Ueberwachungssignal angeschlossen
#define uebsig2_OUT 10    // hier wird das linke Ueberwachungssignal angeschlossen
#define UT1_Status_OUT 9  // hier wird das rechte UT-Kontrolllicht angeschlossen
#define UT2_Status_OUT 8  // hier wird das linke UT-Kontrolllicht angeschlossen

#define NUM_OF_SCHRANKEN 4

//Verbindungspins zum DFPlayer mini
#define DFPlayer_RX A3
#define DFPlayer_TX A2

// Eingangspins
#define ET_PIN 5                    // Einschalttaster
#define UT1_PIN 8                   // Unwirksamkeitstaster rechts
#define UT2_PIN 9                   // Unwirksamkeitstaster links
#define AT_PIN 6                    // Ausschalttaster
#define RS_PIN 7                    // Rangierschalter
#define Strom1_PIN 12               // Stromsensor rechts
#define Strom2_PIN 11               // Stromsensor links
#define LS_PIN 10                   // Freimeldung des Bahnübergangs (Lichtschranke)

#define volume_PIN A6                // Anschluss fuer den Poti zur Lautstärkeregelung

// Define Button objects
Bounce2::Button ET = Bounce2::Button();            // Einschalttaster
Bounce2::Button UT1 = Bounce2::Button();          // Unwirksamkeitstaster rechts
Bounce2::Button UT2 = Bounce2::Button();          // Unwirksamkeitstaster links
Bounce2::Button AT = Bounce2::Button();            // Ausschalttaster
Bounce2::Button RS = Bounce2::Button();            // Rangierschalter
Bounce2::Button Strom1 = Bounce2::Button();    // Stromsensor rechts
Bounce2::Button Strom2 = Bounce2::Button();    //Stromsensor links
Bounce2::Button LS = Bounce2::Button();           // Freimeldung des Bahnübergangs


// Variablen fuer das Blinklicht
int brightnessBlink1 = 0;      // Helligkeit fuer das erste Blinklicht
int brightnessBlink2 = 0;      // Helligkeit fuer das zweite Blinklicht
int Index1 = 0;
int Index2 = 0;
const int periode = 1000;      // Dauer einer Blinkperiode
boolean blinkLichtAn = false;  // Blinklicht beim Start ausgeschaltet
#define AN 4095                // PWM auf maximal
#define AUS 4096               // PWM aus

const PROGMEM byte sinus_tabelle[] = {
    0,  0,  0,  0,  1,  1,  1,  2,  2,  3,  4,  5,  5,  6,  7,  9,
   10, 11, 12, 14, 15, 16, 18, 20, 21, 23, 25, 27, 29, 31, 33, 35,
   37, 39, 42, 44, 46, 49, 51, 54, 56, 59, 62, 64, 67, 70, 73, 76,
   78, 81, 84, 87, 90, 93, 96, 99,102,105,108,111,115,118,121,124,
  127,130,133,136,139,143,146,149,152,155,158,161,164,167,170,173,
  176,178,181,184,187,190,192,195,198,200,203,205,208,210,212,215,
  217,219,221,223,225,227,229,231,233,234,236,238,239,240,242,243,
  244,245,247,248,249,249,250,251,252,252,253,253,253,254,254,254,
  254,254,254,254,253,253,253,252,252,251,250,249,249,248,247,245,
  244,243,242,240,239,238,236,234,233,231,229,227,225,223,221,219,
  217,215,212,210,208,205,203,200,198,195,192,190,187,184,181,178,
  176,173,170,167,164,161,158,155,152,149,146,143,139,136,133,130,
  127,124,121,118,115,111,108,105,102, 99, 96, 93, 90, 87, 84, 81,
   78, 76, 73, 70, 67, 64, 62, 59, 56, 54, 51, 49, 46, 44, 42, 39,
   37, 35, 33, 31, 29, 27, 25, 23, 21, 20, 18, 16, 15, 14, 12, 11,
   10,  9,  7,  6,  5,  5,  4,  3,  2,  2,  1,  1,  1,  0,  0,  0
};

/* Zeitkonstanten

Hier kann das Zeitverhalten des BUEs angepasst werden.

- GrundstellerPeriod: Zeit, nach der der BUE nach dem Schliessen wieder geoeffnet wird, wenn er nicht befahren wurde.
- UTtimeoutPeriod:    Zeit, nachder der Stromsensor wieder aktiviert wird, wenn er mit UT deaktiviert wurde.
- FreiPeriod:         Zeit, die hoechstens zwischen zwei Ausloesungen der Lichtschranke auf dem BUE liegen darf. Nach deren Ablauf wird der BUE frei gemeldet.
- RuhezeitPeriod:     Zeit, waehrend der der Stromsensor nach dem Oeffnen deaktiviert ist. So soll verhindert werden, dass der abfahrende Zug den BUE wieder schliesst.
- ServoDownIncrement  Zeit, die ein Servo später startet als der erste Vorgang um verzögerte Schranken zu erzeugen

*/

const long GrundstellerPeriod = 300000;             // Zeit bis zur Grundstellung des Bahnübergangs (öffnen)
const long UTtimeoutPeriod = 120000;               // Zeit bis zum automatischen Rücknehmen der Unwirksamkeitstaste
const long FreiPeriod = 4000;                    // Zeit, innerhalb der die LS erneut ausgeloest werden muss. Sonst wird BUE frei gemeldet
const long RuhezeitPeriod = 120000;                // Zeit, innerhalb derer der BUE nach Oeffnen nicht auf den Stromsensor reagiert
const long ServoDownIncrement = 250;            // time of an increment of delay for Schranken to go down later than the start time

unsigned long currentMillis = 0;      // Zaehlerstand beim letzten Blinken
unsigned long previousUT1timeoutMillis = 0;  // speichert die Zeit, zu der der UT1 (rechts) Timeout zuletzt ausgeloest wurde
unsigned long previousUT2timeoutMillis = 0;
unsigned long previousGrundstellerMillis = 0; 
unsigned long previousFreiMillis = 0;
unsigned long previousRuhezeitMillis = 0;

boolean SchrankenSetDelay = false;
boolean demoTheDelay = false;

boolean isUT1TimeoutOn = false;
boolean isUT2TimeoutOn = false;

// Variablen für den Zustandsautomaten
uint8_t state = 1;                        // aktueller Zustand
uint8_t next_state = 1;                   // nächster Zustand
uint8_t setup_servo = 0;                  //servo that is being setup

// Lautstärke
int sensorValue = 0;  //value read from volume_PIN from 0 to 1023
uint8_t volumeValue = 0;  //value for volume from 0 to 30

//Ansteuerung DFPlayer mini
SoftwareSerial mySoftwareSerial(DFPlayer_RX, DFPlayer_TX); // RX, TX

#ifdef DFFast
  DFPlayerMini_Fast myDFPlayer;
#else
  DFRobotDFPlayerMini myDFPlayer;
#endif

// Definieren des PWM-Treibers
// called this way, it uses the default address 0x40
Adafruit_PWMServoDriver pwm = Adafruit_PWMServoDriver();

typedef struct  {
   int      PosUnten;        // Position der Stellung "Unten"
   int      PosOben;         // Position der Stellung "Oben"  
   int      updateInterval;   // wie schnell wird die Schranke bewegt
   uint8_t  downdelay;  //delayed start of servo down in 1 sec increments  
} SchrankenDaten;

typedef struct {
  SchrankenDaten schranke[NUM_OF_SCHRANKEN];  // in dieser Konfiguration maximal acht Schranken
} EEPROMPayload ;

typedef struct {
  uint8_t swversion;
  EEPROMPayload payload;
  uint32_t crc;
}  EEPROMData ;

EEPROMData eepromData;

boolean schrankenHoch = true;

typedef struct 
{
   uint8_t Pin;             // Pin, an den die Schranke angeschlossen ist
   int Position;            // Aktuelle Position der Schranke
   int Aenderung;           // Änderung der Position je Druchgang
   unsigned long previousSchrankeMillis = 0;  // letzte Aktualisierung der Position
  //SchrankenDaten& daten;
} Schranke;

Schranke Schrankenset[NUM_OF_SCHRANKEN];

void schrankeInit(uint8_t port) 
{
  Schrankenset[port].Pin = port;
  Schrankenset[port].Aenderung = 3;
  Schrankenset[port].Position = eepromData.payload.schranke[port].PosUnten;
}

void setEEPROMDefaults() {
  for (uint8_t i = 0; i < NUM_OF_SCHRANKEN; ++i) {
      eepromData.payload.schranke[i].PosUnten = 350;
      eepromData.payload.schranke[i].PosOben = 560;
      eepromData.payload.schranke[i].updateInterval = 15;
      eepromData.payload.schranke[i].downdelay = 0; 
    }
    eepromData.swversion = SW_VERSION;
}

void showEEPROMValues(uint8_t pin)
  {
  DEBUG_PRINT("SW-Version: ");
  DEBUG_PRINTLN(eepromData.swversion);
  DEBUG_PRINT("Pin       : ");
  DEBUG_PRINTLN(pin);
  DEBUG_PRINT("Up        : ");
  DEBUG_PRINTLN(eepromData.payload.schranke[pin].PosUnten);
  DEBUG_PRINT("Down      : ");
  DEBUG_PRINTLN(eepromData.payload.schranke[pin].PosOben);
  DEBUG_PRINT("Speed     : ");
  DEBUG_PRINTLN(eepromData.payload.schranke[pin].updateInterval);
  DEBUG_PRINT("Downdelay : ");
  DEBUG_PRINTLN(eepromData.payload.schranke[pin].downdelay);

}

void gotoUnten(uint8_t pin)
{
  pwm.setPWM(Schrankenset[pin].Pin, 0, eepromData.payload.schranke[pin].PosUnten);
  //DEBUG_PRINTLN(eepromData.payload.schranke[pin].PosUnten);
}

void setUnten(uint8_t pin, int increment)
{ 
  if ((eepromData.payload.schranke[pin].PosUnten + increment <= 4095) && (eepromData.payload.schranke[pin].PosUnten + increment >= 0) && (eepromData.payload.schranke[pin].PosUnten + increment <= eepromData.payload.schranke[pin].PosOben)) {
    eepromData.payload.schranke[pin].PosUnten += increment;
  }
}

void gotoOben(uint8_t pin)
{
  pwm.setPWM(Schrankenset[pin].Pin, 0, eepromData.payload.schranke[pin].PosOben);
  //DEBUG_PRINTLN(eepromData.payload.schranke[pin].PosOben);
}

void setOben(uint8_t pin, int increment)
{
  if ((eepromData.payload.schranke[pin].PosOben + increment <= 4095) && (eepromData.payload.schranke[pin].PosOben + increment >= 0) && (eepromData.payload.schranke[pin].PosOben + increment >= eepromData.payload.schranke[pin].PosUnten)) {
    eepromData.payload.schranke[pin].PosOben += increment;
  }
}
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
void loop() {
  // put your main code here, to run repeatedly:
  // Buttonwerte abfragen

  ET.update();
  UT1.update();
  UT2.update();
  AT.update();
  RS.update();
  Strom1.update();
  Strom2.update();
  LS.update();
  
  //read in volume poti and set DFPlayer volume
  sensorValue = analogRead(volume_PIN);
  if (!(volumeValue == map(sensorValue, 0, 1023, 0, 30))) { //only on change
    volumeValue = map(sensorValue, 0, 1023, 0, 30);
    //DEBUG_PRINT("Snd: volume: ");
    //DEBUG_PRINTLN(volumeValue);
    myDFPlayer.volume(volumeValue);  //Set volume value. From 0 to 30
  }
  
  // Aktuelle Zeit speichern
  currentMillis = millis();

  if (servoSetup == true) {
    // Einstellung der Servo Positionen
    //DEBUG_PRINTLN(servoSetupState);
    //DEBUG_PRINTLN(setup_servo);
   switch(setup_servo) {
    case 99: {
      DEBUG_PRINTLN("Servo setup");
      //DEBUG_PRINTLN("Servo 0:"); 
      DEBUG_PRINTLN("up");
      servoSetupState = 1;
      setup_servo = 0;
      pwm.setPWM(blink1_OUT, 0, AN); // an
      pwm.setPWM(blink2_OUT, 0, AUS); // aus
      pwm.setPWM(blink3_OUT, 0, AUS); // aus
      pwm.setPWM(blink4_OUT, 0, AUS); // aus
      pwm.setPWM(uebsig1_OUT, 0, AN); // an Indicate "down" setup
      pwm.setPWM(uebsig2_OUT, 0, AUS); // aus
      pwm.setPWM(UT1_Status_OUT, 0, AUS); // aus
      pwm.setPWM(UT2_Status_OUT, 0, AUS); // aus 
      }
    case 0 ... NUM_OF_SCHRANKEN:
    //case 1:
    //case 2:
    //case 3:
      {
      //DEBUG_PRINT("Servo ");
      //DEBUG_PRINTLN(setup_servo);
      switch(servoSetupState) {
        case 1:
          //DEBUG_PRINTLN("down");
          
          if (ET.pressed()) {DEBUG_PRINTLN("+5");setUnten(setup_servo,+5);};
          if (AT.pressed()) {DEBUG_PRINTLN("-5");setUnten(setup_servo,-5);};
          
          gotoUnten(setup_servo);
    
          if (UT1.pressed() || UT2.pressed() ) {
            DEBUG_PRINTLN("up");
            servoSetupState=2;
            pwm.setPWM(uebsig1_OUT, 0, AUS); // aus
            pwm.setPWM(uebsig2_OUT, 0, AN); // indicate "up" setup
            }
          break;
    
        case 2:
          
          if (ET.pressed()) {DEBUG_PRINTLN("+5");setOben(setup_servo,+5);};
          if (AT.pressed()) {DEBUG_PRINTLN("-5");setOben(setup_servo,-5);};
    
          gotoOben(setup_servo);
          
          if (UT1.pressed() || UT2.pressed() ) {
            DEBUG_PRINTLN("speed");
            servoSetupState=3;
            pwm.setPWM(uebsig2_OUT, 0, AUS); // aus
            pwm.setPWM(UT1_Status_OUT, 0, AN); // indicate speed setup
            }  
          break;
    
        case 3:
          
          if (ET.pressed()) {DEBUG_PRINTLN("+1");setInterval(setup_servo,+1);};
          if (AT.pressed()) {DEBUG_PRINTLN("-1");setInterval(setup_servo,-1);};
    
          Sweep(setup_servo);
          
          if (UT1.pressed() || UT2.pressed() ) {
            DEBUG_PRINTLN("delay");
            servoSetupState=4;
            pwm.setPWM(UT1_Status_OUT, 0, AUS); // aus
            pwm.setPWM(UT2_Status_OUT, 0, AN);  // delay setup step
            }  
          break;
          
        case 4:
          
          if (ET.released()) {DEBUG_PRINTLN("+1");demoTheDelay = true;setdowndelay(setup_servo,+1);};
          if (AT.released()) {DEBUG_PRINTLN("-1");demoTheDelay = true;setdowndelay(setup_servo,-1);};
          
          demoDelay(setup_servo);
          
          if (UT1.pressed() || UT2.pressed() ) { //after step 4, go to the next servo or to the end of the setup
            servoSetupState=1;
            setup_servo++;
            if (setup_servo >= NUM_OF_SCHRANKEN) {setup_servo = 98;} //go to save the setup
            pwm.setPWM(uebsig1_OUT, 0, AN); // down stage setup
            pwm.setPWM(UT2_Status_OUT, 0, AUS); // aus
            switch (setup_servo) {
              //case 0:
              //  pwm.setPWM(blink1_OUT, 0, AN); // aus
              //break;
              case 1:
                pwm.setPWM(blink1_OUT, 0, AUS); 
                pwm.setPWM(blink2_OUT, 0, AN); // aus
              break;
              case 2:
                pwm.setPWM(blink2_OUT, 0, AUS); 
                pwm.setPWM(blink3_OUT, 0, AN); // aus
              break;
              case 3:  
                pwm.setPWM(blink3_OUT, 0, AUS); 
                pwm.setPWM(blink4_OUT, 0, AN); // aus
              break;
              }  
            }
            
          break;
      }
      break;
      }
    case 98: {
      //save the setup for all servos
    
      // clean up setup
        DEBUG_PRINTLN("End Setup");
        StoreToEEPROM();
        servoSetup = false;
        servoSetupState = 1;
        setup_servo = 0;
        state = 1;
        pwm.setPWM(blink1_OUT, 0, AUS); // aus
        pwm.setPWM(blink2_OUT, 0, AUS); // aus
        pwm.setPWM(blink3_OUT, 0, AUS); // aus
        pwm.setPWM(blink4_OUT, 0, AUS); // aus
        pwm.setPWM(uebsig1_OUT, 0, AUS); // aus
        pwm.setPWM(uebsig2_OUT, 0, AUS); // aus
        pwm.setPWM(UT1_Status_OUT, 0, AUS); // aus
        pwm.setPWM(UT2_Status_OUT, 0, AUS); // aus
      break;
    }
   }
  }
  else {
    // Normaler Betrieb
 
   switch (state) {
    case 1:
      // Zustand: Ruhezustand
      
      // Zustandsausgabe
      //DEBUG_PRINTLN("Ruhezustand");
      
      if (RS.isPressed()) {
      //if (RS.pressed()) {
        next_state = 2;
        DEBUG_PRINTLN("1-->2");
        blinkLichtAn = true;
      }
      else if (ET.pressed()) {
        next_state = 3;
        DEBUG_PRINTLN("1-->3 ET");
        enableGrundsteller();
        blinkLichtAn = true;
      }
      else if ((isUT1TimeoutOn==false)&&(Strom1.pressed() || Strom1.isPressed() )) {
        next_state = 3;
        DEBUG_PRINTLN("1-->3 Strom1");
        enableGrundsteller();
        blinkLichtAn = true;
      }
      else if ((isUT2TimeoutOn==false)&&(Strom2.pressed() || Strom2.isPressed() )) {
        next_state = 3;
        DEBUG_PRINTLN("1-->3 Strom2");
        enableGrundsteller();
        blinkLichtAn = true;
      }
      else if (UT1.pressed()) {
        setUTTimeout(1);
        next_state = 1;
      }
      else if (UT2.pressed()) {
        setUTTimeout(2);
        next_state = 1;
      }
      
      else {
       next_state = 1; 
      }
      break;
    case 2:
      // Zustand: BÜ schließen rangieren
      // Zustandsausgabe
      //bin_out(state);
      //DEBUG_PRINTLN("BÜ schließen rangieren");
      
      next_state = 4;
      DEBUG_PRINTLN("2-->4");
      
      //start sound
      myDFPlayer.loop(1);
      #ifdef DFFast
        myDFPlayer.startRepeatPlay();
      #endif
      schrankenHoch = false;
      SchrankenSetDelay = true;
      
      break;
    case 3:
      // Zustand: BÜ schließen normal
      // Zustandsausgabe
      //DEBUG_PRINTLN("BÜ schließen normal");
      
      next_state = 5;
      DEBUG_PRINTLN("3-->5");
      
      //start sound
      //DEBUG_PRINTLN("Snd: loop");
      myDFPlayer.loop(1);
      #ifdef DFFast
        myDFPlayer.startRepeatPlay();
      #endif
      
      schrankenHoch = false;
      SchrankenSetDelay = true;
      
      break;
    case 4:
      // Zustand: BÜ geschlossen rangieren
      // Zustandsausgabe
      //bin_out(state);
      //DEBUG_PRINTLN("BÜ geschlossen rangieren");
      
      if (RS.isPressed()) {
        next_state = 4;
        //DEBUG_PRINTLN("4-->4");
      }
      else {
       next_state = 9; 
       DEBUG_PRINTLN("4-->9");
      }
      
      break;
    case 5:
      // Zustand: BÜ geschlossen normal
      // Zustandsausgabe
      //DEBUG_PRINTLN("BÜ geschlossen normal");
      
      if (RS.isPressed()) {
        next_state = 4;
        DEBUG_PRINTLN("5-->4");
      }
      else if (LS.pressed()) {
       next_state = 6; 
       DEBUG_PRINTLN("5-->6");
       enableFrei();
      }
      else if (AT.pressed() || checkGrundsteller() == true) {
        next_state = 7;
        DEBUG_PRINTLN("5-->7 AT");
      }
      else {
        next_state = 5;
      }
      break;
    case 6:
      // Zustand: BÜ geschlossen, befahren
      // Zustandsausgabe
      //DEBUG_PRINTLN("BÜ geschlossen, befahren");
    
      if (RS.isPressed()) {
        next_state = 4;
        DEBUG_PRINTLN("6-->4 RS");
      }
      else if (checkFrei()==true) {
       next_state = 7; 
       DEBUG_PRINTLN("6-->7");
      }
      else {
        next_state = 6;
      }
      break;
    case 7:
      // Zustand: BÜ öffnen
      // Zustandsausgabe
      //DEBUG_PRINTLN("BÜ öffnen");
      
      next_state = 8;
      DEBUG_PRINTLN("7-->8");
      blinkLichtAn = false;
      
      schrankenHoch = true;
      
      // stop sound
      //myDFPlayer.play(1);
      myDFPlayer.stop();
      
      enableRuhezeit();  // Starte Timer fuer Ruhezeit
      
      break;
    case 8:
      // Zustand: Ruhezeit
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

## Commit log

2021-05-17 added manuals
    add drill template and pcb soldering manual
2021-05-17 added ordering lists
    added Reichel csv files for direct ordering components
    [Bue-v2.csv, rangierbox.csv, sensorbox.csv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]
2021-10-11 Programming instructions for Arduino
2021-10-11 added Arduino programming
2021-10-16 dffast driver
2021-10-16 Create Programmierung Arduino für Bahnübergangssteuerung.pdf
2021-10-18 Revert "Delete Programmierung Arduino für Bahnübergangssteuerung.pdf"
    This reverts commit 76058ff07bfd1d54a2f4ac115b1b7e38dc75fe13.
2021-12-06 hw3
    Loconet and bord redesign
    [bue_steuerung_3.brd, bue_steuerung_3.sch]
2022-08-26 Added HW and SW versions 1 and 2
    [bue_steuerung.brd, bue_steuerung.sch]

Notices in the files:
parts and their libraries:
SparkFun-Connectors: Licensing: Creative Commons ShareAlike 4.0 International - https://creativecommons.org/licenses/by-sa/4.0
